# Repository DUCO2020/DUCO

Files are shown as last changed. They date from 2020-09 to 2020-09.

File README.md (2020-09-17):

DUCO

=======

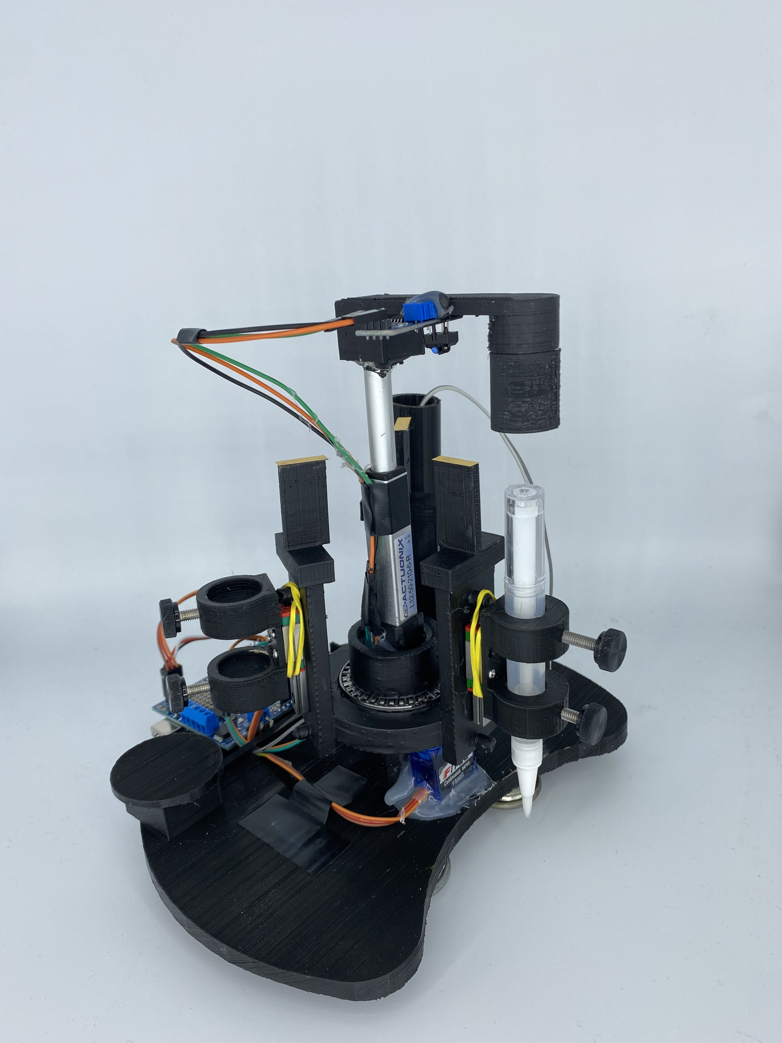
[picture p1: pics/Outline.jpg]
Art


DUCO is an open-source, tool switchable robotic system capable of drawing multi-layer circuits on versatile vertical surface. Assembling parts are highly accessible and low cost. It's inspired by Sandy Noble's work [*Polargraph*](https://github.com/euphy/polargraph)

DUCO is developed for large scale circuits fabrication, but maintaining considerable local precision and resolution. It has default optimal configuration for several drawing substrates - wall paper, glass, wood and etc, also supporting other substrate exploitation.

While linear actuator, laser cutter are well explored in this project, DUCO still have the extensible ability to welcomes all other tools like vinyl cutter and dispenser.

## High-level ability

* Two-stepper locomotion system with well set Cartesian-to-polar solution
* Meter size canvas
* Up to 3 tools mounting platform.
* Ink loaded pen based fabrication with good line quality
* Highly user extensible. User can explore any tools, inks and drawing substrates
* Autonomous robotic system with pen switch, pen pressure function enabled
* Enough spare GPIOs. User can develop new functions since only a few pins are occupied

## What we offer here

This resposity contains Graphical User Interface, Arduino operation firmware and all design files that our team used to test and explore this platform.

* **DucoFirmware** C code on [Arduino](https://www.arduino.cc/), currently supporting UNO to control all motion and actuation commands. 
* **DucoGUI** developed interface based on [Processing](https://processing.org/) framework, allowing user to interact with DUCO like selecting tools, uploading design files and start a drawing task.
* **DucoTest** contains all design files in SVG format that our team used.
* **DucoModels** gives access to all 3D model parts we used.
* **DUCO_BOM** inventory list.

## Put parts together

1. Before moving to run DUCO, you should first have all assembling parts ready. You can either use prototype files in Duco_models folder or design your own 3D model as long as you figure out the correct dimension for assembling.

2. After you get all these accessories printed, first thing you may want to do is assembling the centre platform, we have a figure that you can refer to when you do that.

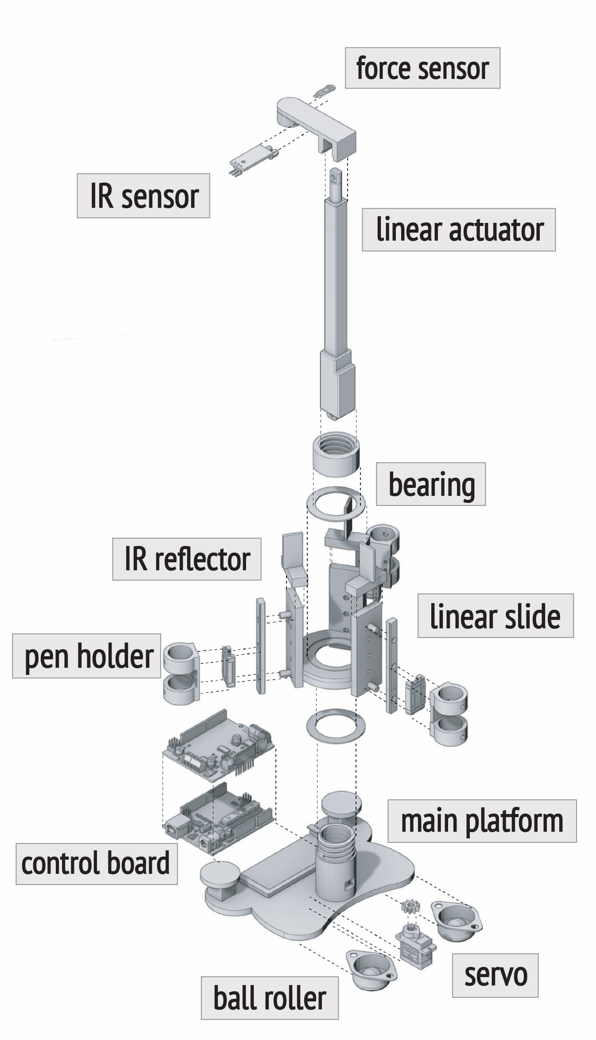
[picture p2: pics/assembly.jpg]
   

3. Subsequently, use hot glue to attach the printed anchor with your steppers( for our choice we use 4-wire [NEMA 17](https://www.banggood.com/3D-Printer-High-Torque-17-Stepper-Motor-300mN-1_5A-2-phase-4-wire-p-1064247.html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), it has a good rated current/ voltage about 5 volts which is suitable for a constant voltage driver.) Then you put a proper size of gear on the stepper driving axis for we need it to hang a belt.

## Hardware setup

1. The very first thing you need to do here is working out what size of your design is and choose a proper operiting area, after which you need to fix the two anchors on the top line. Remember to spare some space both horizontally and vertically, also collecting the dimensional data of your system

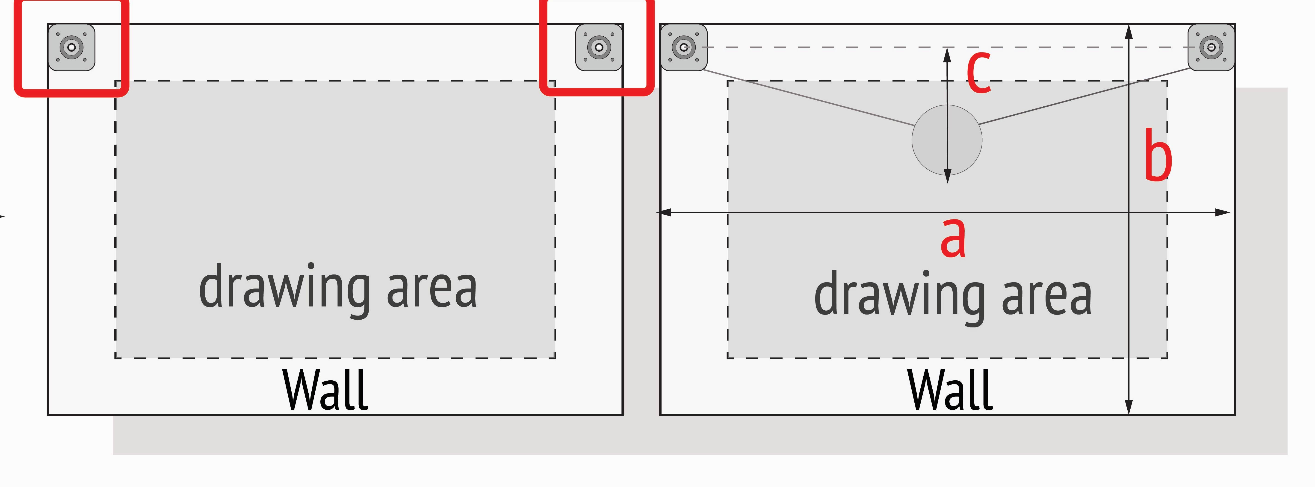
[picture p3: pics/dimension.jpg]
   

2. Moving forward, two [GT2 timing belts](https://www.amazon.com/Printing-Zeelo-Fiberglass-Rostock-Printers/dp/B0897CJKS1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) are involved. one end of each is both connected with center platform and the other one is tied to hold a weight. They are hanged on two anchors respectively. Note, choosing correct length is important, neither too short (not covering enough moving space) nor too long (causing loosen belts when the weight hits ground)

3. Now attach your Arduino Uno with motor shield. Our firmware is based on [Adafruit motor shield v2](https://learn.adafruit.com/adafruit-motor-shield-v2-for-arduino/overview), a typical constant voltage driver. If you want a more stable torque output, you may consider constant current driver AKA chopper driver. However using other shield requires you to modify the firmware configuration as well.

4. Uno and motor shield becomes control partner and you can stick them "in the brain" of our platform and also put metal stickers on the reflecters.

5. One last step you carrry out is to do wiring up

   - COMs on the shield: usually the stepper is together with 4-color wire, green/black is one couple, blue/red is another. each couple should be connected to one COM on the shield. One stepper is supposed to be connected to the same side's COMs, i.e. for one stepper COM1/2 are used, COM3/4 are responsible for another one.
   - Power port on the shield: + to 5V on DC, - to GND on DC
   - IR: Vcc to 5V on the shield, GND to GND on the shield, SIG to analog pin 1
   - Continuous servo:  to servo port 1 on the shield.
   - Linear actuator: to servo port 2 on the shield.
   - Arduino Uno: to your laptop with USB cable.

## Inventory 

We have an Excel table listing all materials that you may need.

## Q&A

1. Platform moving behavior is wrong.

   Probably something wrong with stepper wiring. Try to swap the connection that is under the same COM

2. When switching tool, the platform keeps rotating then stop and fails to locate a mounting slot.

   It's caused by unsuitable threshold set. Several reasons may result in this:

   - The metal sticker and the IR is not well aligned vertically
   - The metal sticker is not reflective enough
   -  Distance between IR and stickers is too far away.

   We recommend you to open an Arduino sketch and take a look at the IR feedback from analog pin 1. When sticker and IR are well aligned the value should be under 500, typically 200-350. If this is not your case, record your typical value and subtracted by 100-150. Then set this value to variables in Firmware: `thresholdxHigh`(x= 1,2,3) and try again.

   Note: three slots typical value should be almost the same (the program needs this assumption) and a good typical value is always much smaller than 1023. Adjust your `DEFAULT_UP_POSITION` in Firmware to achieve this.

3. Steppers are heating up.

   - The first thing you are looking into should be the supply voltage. Generally when it's higher than the rated voltage of your steppers, overheating takes place. Be sure to give correct voltage supply.
   - When the wires between two steppers and motor shield are not the same length. Wires are introducing extra resistance to your steppers, thus do your best to balance two wires' length(resistance)

4. Linear actuator shows no response or misbehaves.

   Basically caused by unstable connection between shield and linear actuator. Use some insulated tape to enhance the connection and make sure there's no other wires around that of linear actuator. Give it independent space since it's easy to be disturbed.

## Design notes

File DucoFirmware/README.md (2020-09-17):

# DUCOFirmware

This is the Arduino Uno folder that needed to be burnt in

## How to use it

- Download or clone this folder to your local. Make sure you get rid of the surfix "-master" generated by Github, since Arduino requires the folder name should match the main file name.
- connect your device to laptop, find the correct Serial Port on Arduino IDE "tools" sidebar. Then upload this Firmware into your device. At last make sure Arduino IDE is **NOT** occupying the Port after uploading, otherwise GUI Serial Port connection on Processing will fail.

## Functionality we provide

Refer to Section 5 of the paper

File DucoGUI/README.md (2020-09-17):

# DUCOGUI

This is the GUI folder for DUCO, it's based on Processing.

## How to use it

- Download or clone this folder to your local. Make sure you get rid of the surfix "-master" generated by Github, since Processing requires the folder name should match the main file name.
- If you have nothing to develop or tune, directly click on run. Then the interface will pop-up.

## Introduction to the Interface

- please refer to Section 6 of the paper

## Note

- photo paper/wood is a bit hard to fabricate circuits, so we enable Microstep. However, it's a super slow process without any speed control.
- Welcome page has a **Pen Position** menu. That part of functionality is not in use right now. It was aimed at making different mounting slots distinguishable by DUCO. However it requires different reflective stickers and responding different threshold set in Firmware. If you are interested in making it work, contact us!

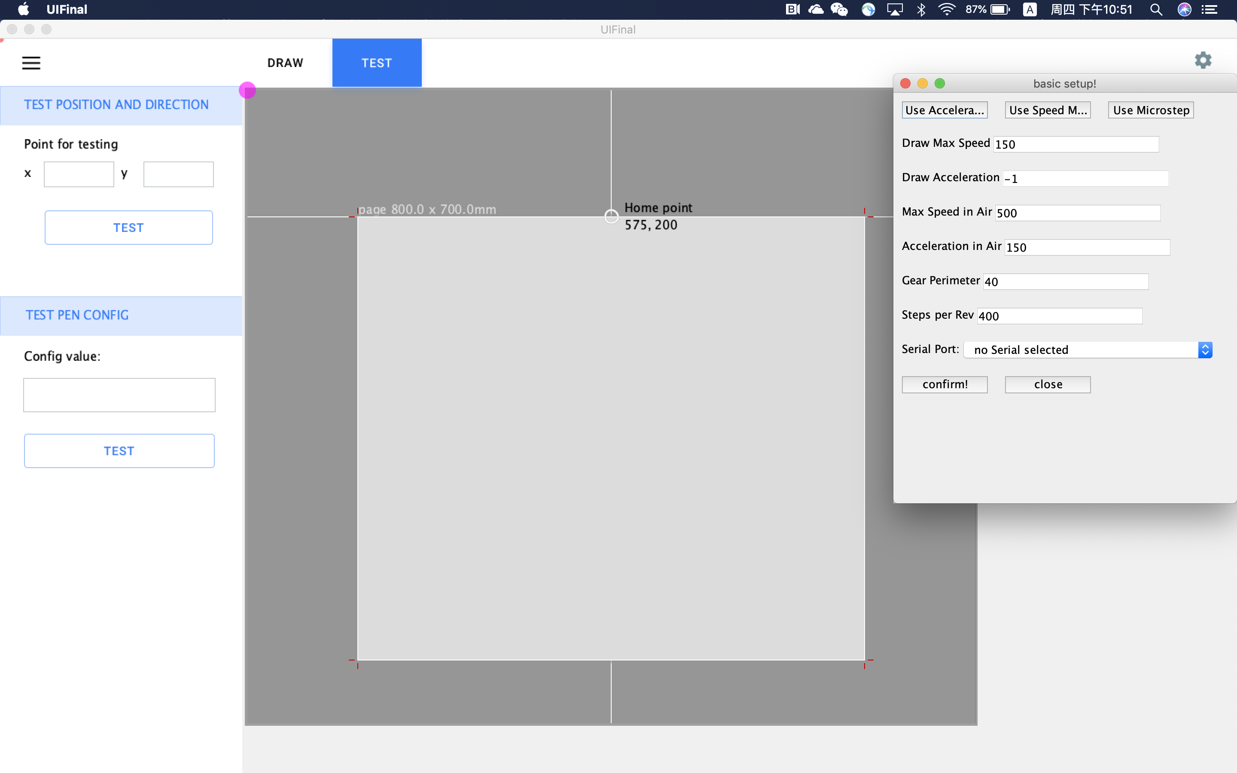
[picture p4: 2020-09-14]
DucoGUI/UI_Look/advancedSettings.png

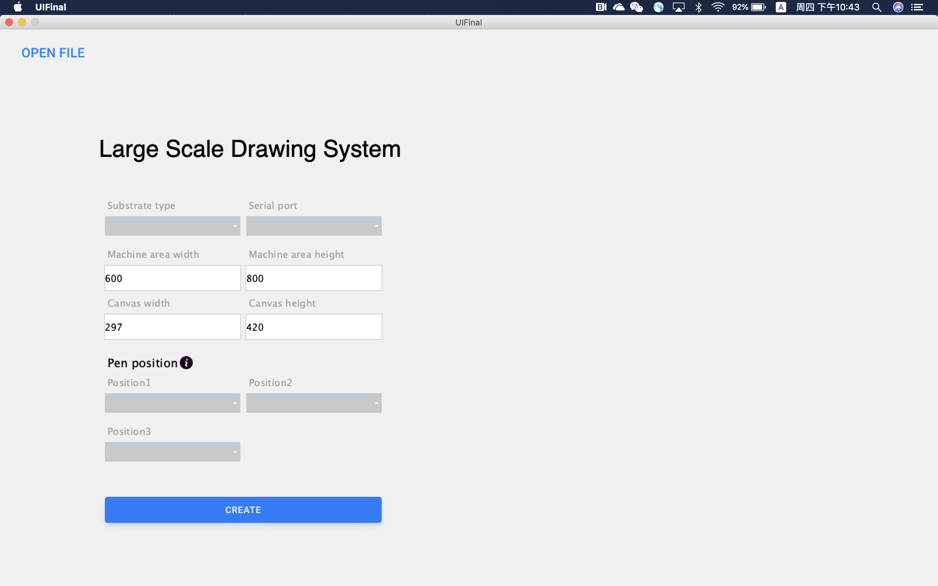
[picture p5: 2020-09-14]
DucoGUI/UI_Look/welcomePage.png

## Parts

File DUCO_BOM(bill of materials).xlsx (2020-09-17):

linear actuator | 1 | https://www.actuonix.com/L12-R-Linear-Servo-For-Radio-Control-p/l12-r.htm | 70 |  | L12 -R Micro Linear Servo - 50mm - 210:1 - 6 vdc
linear slide | 3 | https://www.amazon.com/gp/product/B07G3D6QHQ/ref=ppx_yo_dt_b_asin_title_o05_s00?ie=UTF8&psc=1 | 7.99 |  | LWL7B Miniature Linear Rail Guide 7mm Width Slide Block (40MM)
thumb nuts | 6 | https://www.mcmaster.com/catalog/126/3400 | 8.03/10 | 0.8each | Reinforced Plastic Knurled-Head Thumb Nuts 93886A230
thumb screw | 6 | https://www.mcmaster.com/catalog/126/3266 | 5.38/10 | 0.54 each | Metric Knurled Plastic-Head Thumb Screws 96016A559
continuous servo | 1 | https://www.amazon.com/gp/product/B079FRHBTR/ref=ppx_yo_dt_b_asin_title_o06_s00?ie=UTF8&psc=1 | 20.99/4 | 5.2 each | Geekstory Feetech FS90R 360 Degree Continuous Rotation Micro Servo Motor
rubber band | several | https://www.amazon.com/gp/product/B074B1KCXD/ref=ppx_yo_dt_b_asin_title_o01_s00?ie=UTF8&psc=1 | 5.49/bag |  | AmazonBasics 26543 Assorted Size and Color Rubber Bands
reflective paper | 1 | https://www.amazon.com/Silhouette-MEDIA-GLD-ADH-Printable-Gold-Foil/dp/B008RX1B28 | 9.64 |  | Silhouette Printable Gold Foil
jumper wire | several | https://www.amazon.com/gp/product/B07GD2BWPY/ref=ppx_yo_dt_b_asin_title_o02_s00?ie=UTF8&psc=1 | 5.79/120 |  | EDGELEC 120pcs Breadboard Jumper Wires 20cm
rotational bearing | 2 | https://www.mcmaster.com/catalog/126/1274 | 3.4 |  | Needle-Roller Thrust Bearings 5909K37
aruduino board (UNO) | 1 | https://www.amazon.com/Arduino-A000066-ARDUINO-UNO-R3/dp/B008GRTSV6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 | 22.79 |  | ARDUINO UNO R3
motor shield | 1 | https://www.amazon.com/gp/product/B00JI99DX4/ref=ppx_yo_dt_b_asin_title_o04_s01?ie=UTF8&psc=1 | 24.42 |  | Adafruit Motor/Stepper/Servo Shield for Arduino v2 Kit
force resistive sensor | 1 | https://www.tekscan.com/products-solutions/force-sensors/ess301 | 73.3/4 pieces | 18.325 | FlexiForce ESS301 Sensor
free weight | 2 | https://www.amazon.com/Ajax-Scientific-Economy-Hook-Weight/dp/B00EPQF4BK | 15.37 |  | Ajax Scientific ME180-0500 Economy Hook Weight, 500g
stepper motor | 2 | https://www.banggood.com/3D-Printer-High-Torque-17-Stepper-Motor-300mN-1_5A-2-phase-4-wire-p-1064247.html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 | 11.46 |  | High Torque 17 Stepper Motor 300mN 1.5A 2-phase 4-wire
IR sensor | 1 | https://www.amazon.com/gp/product/B07C69N65P/ref=ppx_yo_dt_b_asin_title_o00_s00?ie=UTF8&psc=1 | 12.99/10 piece | 1.3 each | OSOYOO 10PCS TCRT5000 Infrared Reflective IR Photoelectric Switch Barrier Line Track Sensor Module for Arduino Smart Car Robot with 5 8Pin Female to Female Jumper Wires
optional rollar | 2 | https://www.amazon.com/gp/product/B07ZHYFDW8/ref=ppx_yo_dt_b_asin_title_o03_s00?ie=UTF8&psc=1 | 10.99/8 | 1.37 each | MoKell 8pcs CY-15H 5/8-inch Bearing Steel Roller Ball
nano tape | 1 | https://www.amazon.com/gp/product/B07X32RKBN/ref=ppx_yo_dt_b_asin_title_o07_s00?ie=UTF8&psc=1 | 16 |  | GLUIT- Premium Nano Tape 17.5 lbs
belts | 1 | https://www.amazon.com/gp/product/B076LRL34G/ref=ppx_yo_dt_b_asin_title_o07_s00?ie=UTF8&psc=1 | 12.98 |  | SCStyle 10 Meters GT2 2mm Pitch 6mm Wide Timing Belt for 3D Printer CNC by SCStyle
silver nanoparticle ink | 1 | https://www.dycotecmaterials.com/product/dm-sij-3200/ | 428/100g |  | Dycotec DM-SIJ-3200 is a nanosilver ink-jet printable ink
dielectric ink | 1 | https://www.norlandprod.com/adhesives/NEA%20121.html | 47four onces |  | Norland Electronic Adhesive 121
pully | 1 | https://www.amazon.com/gp/product/B085QKS6X8/ref=ppx_yo_dt_b_asin_title_o03_s00?ie=UTF8&psc=1 | 12.99 |  | Befenybay 2Kit 2GT Synchronous Wheel Aluminum Timing Pulley with 2pcs Length 200mm Width 6mm Belt (20-48T-5B-6)
optional
laser cutter head 7W | 1 | https://www.amazon.com/gp/product/B088FJJ66M/ref=ppx_yo_dt_b_asin_title_o09_s00?ie=UTF8&psc=1 | 78 |  | NEJE 7W Engraving Module,2.5W Output Power,Suitable for NEJE Master 2 Engraving Machine,CNC Machine/Router/Arduino/3D Printer,etc.(2.5W Module)
laser cutting head 20W | 1 | https://www.amazon.com/gp/product/B088FGJBJ7/ref=ppx_yo_dt_b_asin_title_o09_s00?ie=UTF8&th=1 | 149 |  | NEJE 20W Engraving Module,5.5W Output Power,Suitable for NEJE Master 2 Engraving Machine,CNC Machine/Router/Arduino/3D Printer,etc.(5.5W Module)
pen | 1 | https://www.amazon.com/Montana-Cans-MXA324048-Acrylic-Marker/dp/B006ZM19IE | 4.25 |  | Montana Cans Montana Acrylic Empty, 2mm Paint Marker
brush | 1 | https://www.amazon.com/gp/product/B07W8T9CDQ/ref=ppx_yo_dt_b_asin_title_o00_s01?ie=UTF8&psc=1 | 9.98/12 | 0.83 | 12 Pack 3 ml Transparent Twist Pens
DV power supply | 1 | https://www.amazon.com/gp/product/B073TW8H2S/ref=ppx_yo_dt_b_asin_title_o05_s00?ie=UTF8&psc=1 | 69.99 |  | DC Power Supply Adjustable (0-30 V 0-10 A), Eventek KPS3010D Variable Switching Regulated Digital Power Supply
microscope | 1 | https://www.amazon.com/gp/product/B07PVMRZQH/ref=ppx_yo_dt_b_asin_title_o00_s00?ie=UTF8&psc=1 | 41.99 |  | Wireless Digital Microscope Handheld USB HD Inspection Camera
craft knife | 1 | https://www.dickblick.com/products/x-acto-1-knife/ | 4.16 |  | X-Acto #1 Knife
dispenser | 1
3D printed parts
main body_down | 1
mainbody_cap | 1
main body_up | 1
pen holder | 3
IR reflector | 3
linear actuator cap | 1
stepper holder

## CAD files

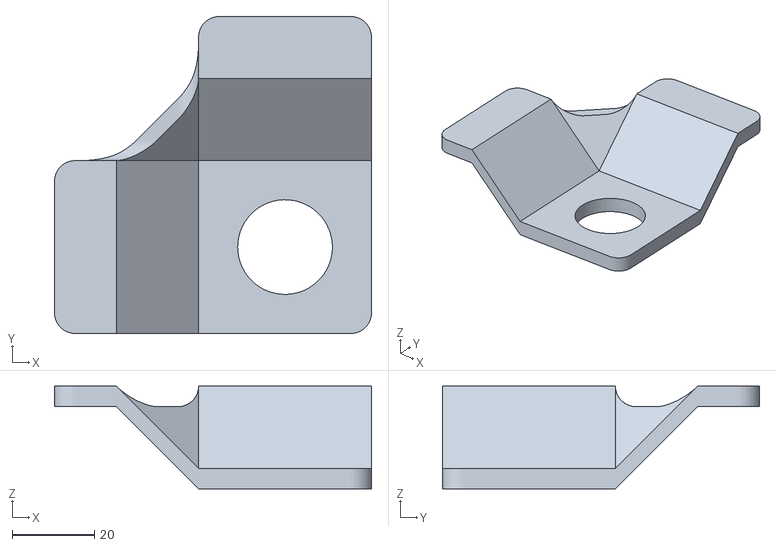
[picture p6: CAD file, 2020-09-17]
DucoModels/Steppermotor_holder.stl
77.0 x 77.0 x 25.0

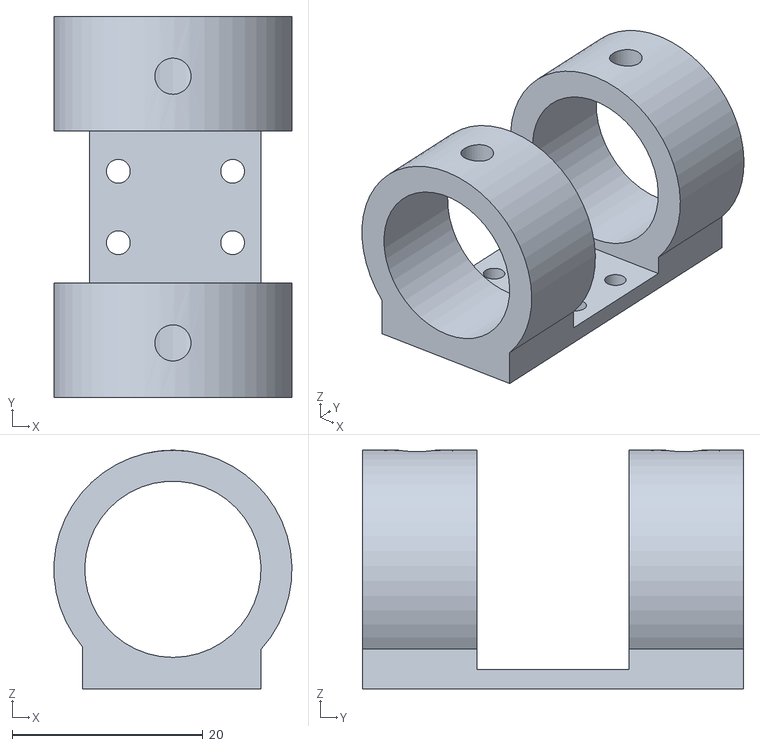
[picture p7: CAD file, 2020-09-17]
DucoModels/Pen_holder_big.STL
25.0 x 40.0 x 25.0

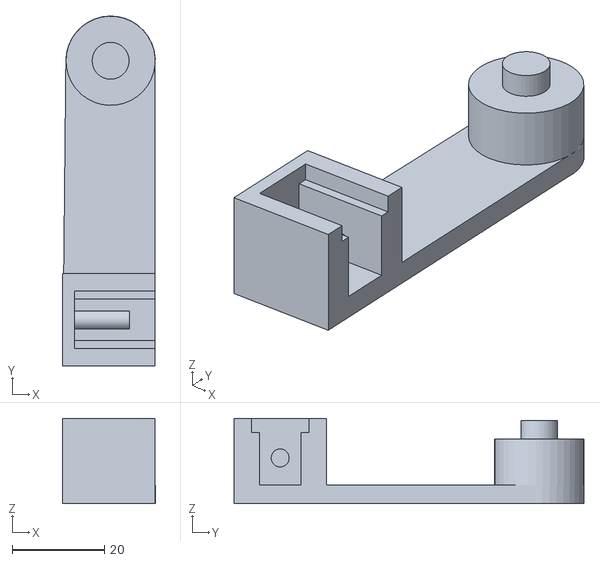
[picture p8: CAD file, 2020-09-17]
DucoModels/linearactuator_cap.STL
20.0 x 75.8 x 18.5

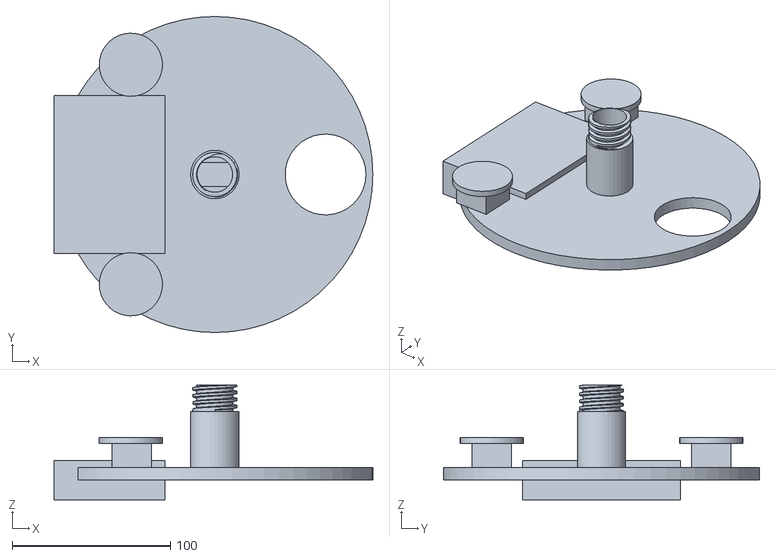
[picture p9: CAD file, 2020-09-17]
DucoModels/midplate_down_v2.STL
201.7 x 200.0 x 72.5

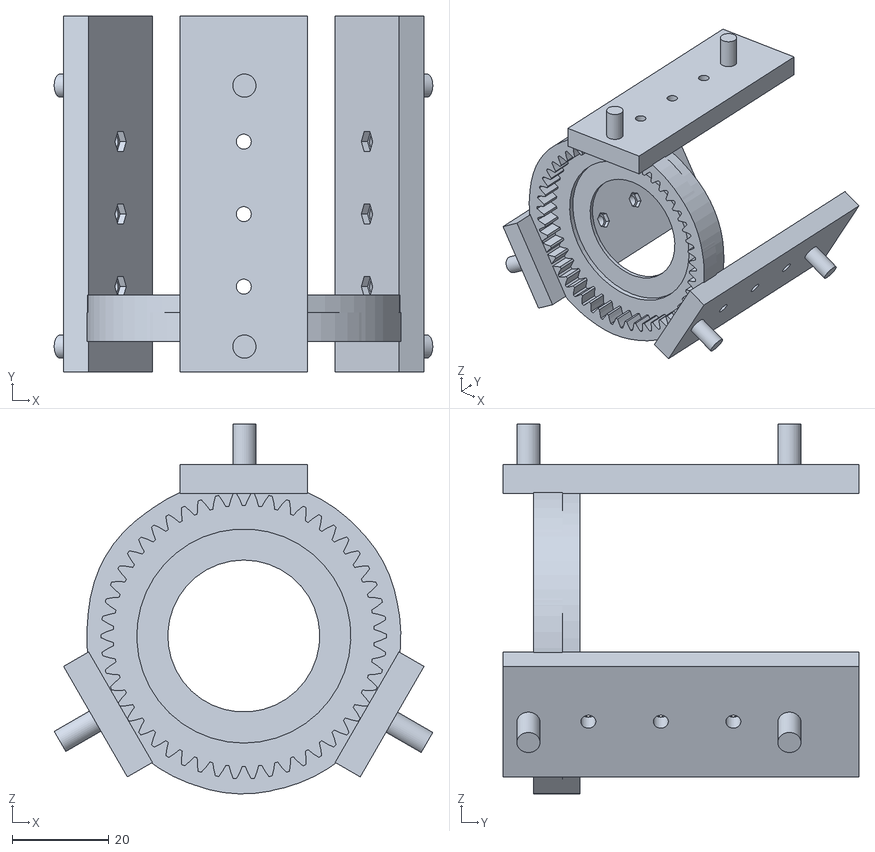
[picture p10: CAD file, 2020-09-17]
DucoModels/midplate_top.STL
78.3 x 73.7 x 76.5

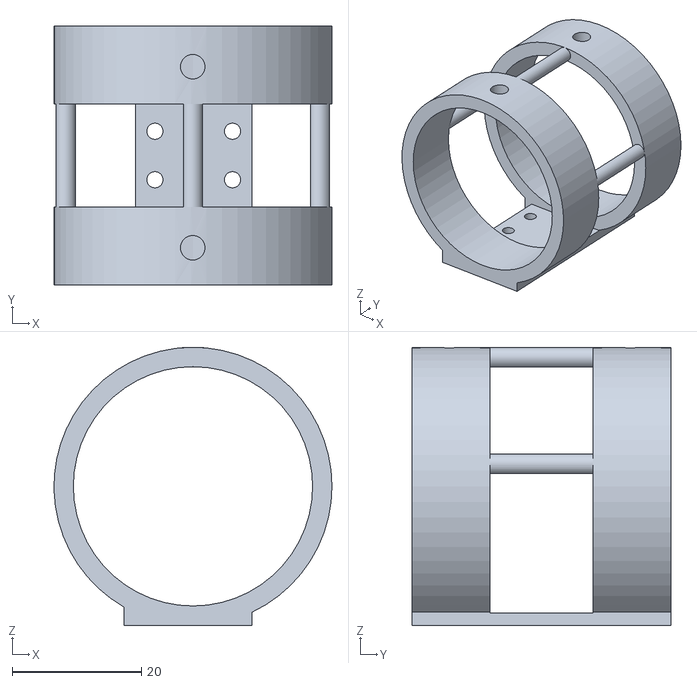
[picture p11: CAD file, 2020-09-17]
DucoModels/Microscope_holder.STL
43.0 x 40.0 x 43.0

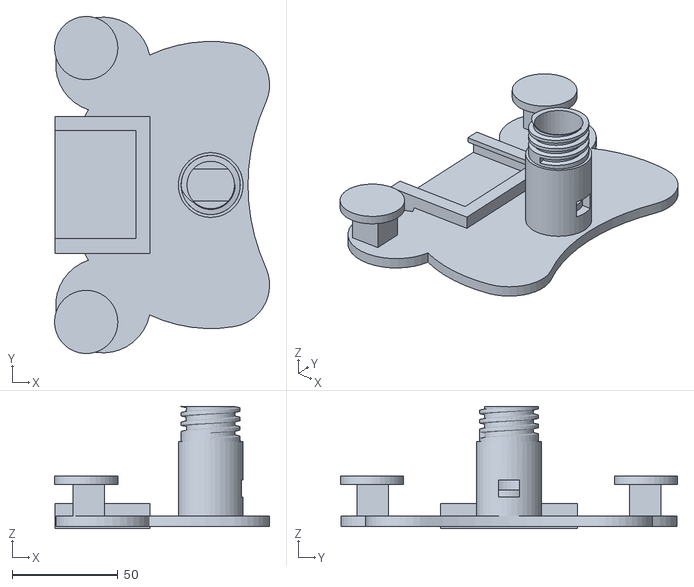
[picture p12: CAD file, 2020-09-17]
DucoModels/midplate_bottom_v1.STL
101.8 x 159.7 x 58.0

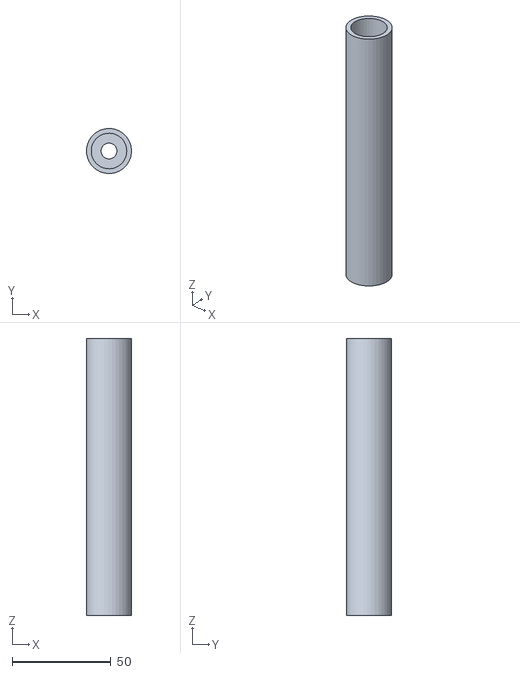
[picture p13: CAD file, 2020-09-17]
DucoModels/ultraviolet_holder.STL
22.8 x 22.8 x 140.0

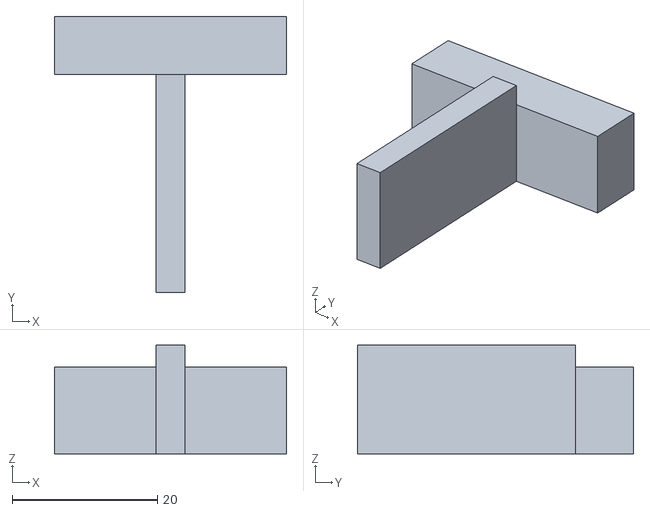
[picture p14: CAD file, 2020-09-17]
DucoModels/IRsensor_cap.STL
32.0 x 38.0 x 15.0

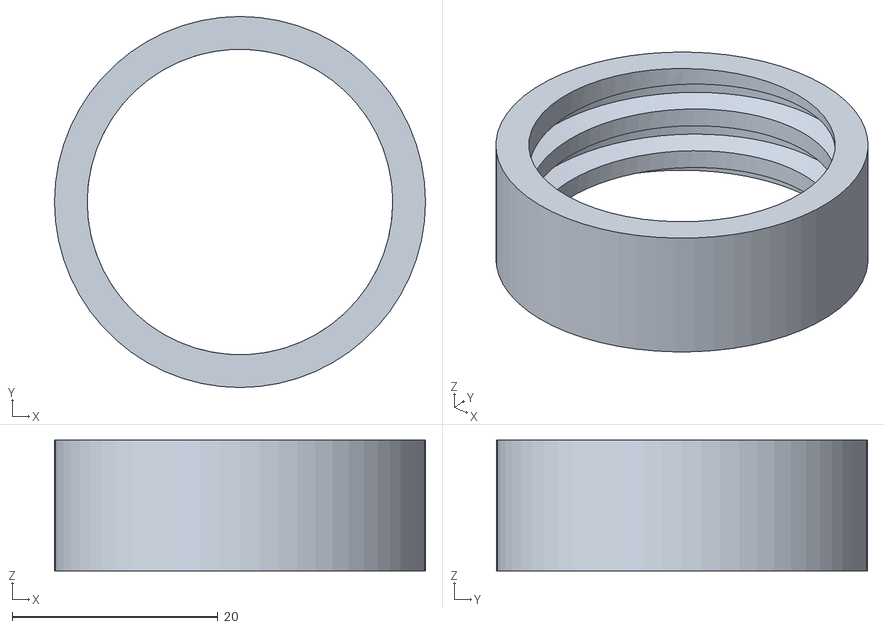
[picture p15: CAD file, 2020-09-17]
DucoModels/midplate_top_holder.STL
36.0 x 36.0 x 12.7

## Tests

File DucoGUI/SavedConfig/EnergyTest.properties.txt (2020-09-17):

#   ***  DUCO properties file   ***  
#Mon Sep 07 15:36:12 EDT 2020
DUCO.machine.width=1150
DUCO.homepoint.y=300
DUCO.page.width=800
DUCO.page.position.y=300
DUCO.motors.inAirMaxSpeed=500
DUCO.speedMode=1
DUCO.vector.position.y=280.75
DUCO.machine.height=1000
DUCO.motors.usingMicrostep=false
DUCO.vector.position.x=367.48
DUCO.motors.inAirAccel=150
DUCO.motors.maxSpeed=300
DUCO.motors.stepsPerRev=400.0
DUCO.motors.mmPerRev=40.0
DUCO.page.height=700
DUCO.motors.accel=100

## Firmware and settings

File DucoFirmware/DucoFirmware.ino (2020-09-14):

/**
*  DUCO - CORE
*  the main file to run this firmware
*  Make sure you have correct hardware setup and wiring
*  then this firmware works reliably
*/
#ifndef MICROCONTROLLER
#define MICROCONTROLLER MC_UNO
#endif
#define ADAFRUIT_MOTORSHIELD_V2
#include <Wire.h>
#include <Adafruit_MotorShield.h>
#define VECTOR_LINES
#define MC_UNO 1

#include <AccelStepper.h>
#include <Servo.h>
#include <EEPROM.h>
#include "EEPROMAnything.h"
const String FIRMWARE_VERSION_NO = "2";
//  EEPROM addresses
const byte EEPROM_MACHINE_WIDTH = 0;
const byte EEPROM_MACHINE_HEIGHT = 2;
const byte EEPROM_MACHINE_MM_PER_REV = 14; // 4 bytes (float)
const byte EEPROM_MACHINE_STEPS_PER_REV = 18;

const byte EEPROM_MACHINE_MOTOR_SPEED = 20; // 4 bytes float
const byte EEPROM_MACHINE_MOTOR_ACCEL = 24; // 4 bytes float

const byte EEPROM_MACHINE_HOME_A = 28; // 4 bytes
const byte EEPROM_MACHINE_HOME_B = 32; // 4 bytes

const byte EEPROM_PENLIFT_DOWN = 36; // 2 bytes
const byte EEPROM_PENLIFT_UP = 38; // 2 bytes

const byte EEPROM_PEN_MODE = 40; // 2 bytes int
const byte EEPROM_SPEED_MODE = 42; // 1 byte  only 2bits used
//const byte EEPROM_PLATFORM = 43;
/**
 *       SpeedMatch  Acceleration       utility
 * 00       false        false       microstepping
 * 01       false        true         Interleave
 * 10       true         false       under experiment
 * 11       true         true        under experiment
 */

int numberResend=0; // resend times counter
// motor setup
const int stepTypeM = MICROSTEP;  //resolution test
const int stepTypeI = INTERLEAVE;
int currentMotorMode = 0;

// Pen gesture control variables
Servo penHeight;
const int DEFAULT_PEN_MODE = 0;
const int DEFAULT_DOWN_POSITION = 1100; //pulse width in micro sec  
const int DEFAULT_UP_POSITION = 1750; // with new plugs
int upPosition = DEFAULT_UP_POSITION; // not used in PenMode 1
int downPosition = DEFAULT_DOWN_POSITION; // become percentage value in penMode 1
int penMode = DEFAULT_PEN_MODE; //0:linear actuator control; 1: laser cutter control; 2:pen force
static int penLiftSpeed = 110; // ms between steps of linear actuator
boolean isPenUp = true; // initial state should be up
byte const PEN_HEIGHT_SERVO_PIN = 10; //UNL2003 driver uses pin 9
byte const LASER_PIN = 3;

// pen force control
int safetyCheck = 1200;  // change along with different pen length/setup
int dynamicDownPos = DEFAULT_UP_POSITION; // used in penforce function
int ResHig = 1000; // high bound 150 Kohms with cheap FSR   600 with finer FSR
int ResLow = 100; // low bound 10 Kohms with cheap FSR   60 with finer FSR
const int power = 4;
const int FSR = 2;  // 0 is not reliable!!!!!

// platform rotate
Servo platRot;
boolean lastFound = false;
const int IR = 1;
byte const PLAT_ROTATE = 9;
const int Clockwise = 73;
const int stop = 90;
const int switchTimeout = 7000;
const int interval = 30;
const int weight = 0.3; // to guarantee fast response, not too large
int lastPer = 1000;
int threshold1High = 500; int threshold1Low = 0;  //tool1 with foil surface
int threshold2High = 500; int threshold2Low = 0;  //tool1 with foil surface
int threshold3High = 500; int threshold3Low = 0;  //tool1 with foil surface
//int threshold1High = 70; int threshold1Low = 0;  //tool1 with foil surface
//int threshold2High = 590; int threshold2Low = 560; //tool2 with white surface
//int threshold3High = 750; int threshold3Low = 720; //tool3 with black surface


// default values for wrong setup situation
static int defaultMachineWidth = 650;
static int defaultMachineHeight = 650;
static float defaultMmPerRev = 32;
static int defaultStepsPerRev = 200;
static int defaultSpeedMatch = false;
static int defaultusingAcceleration = true;
static float defaultMaxSpeed = 1000; // for Accel library one time setup
static float defaultMaxAcceleration = 800; // for Accel Library one time setup

// values used in RUNTIME
int machineWidth = defaultMachineWidth;
int machineHeight = defaultMachineHeight;
float mmPerRev = defaultMmPerRev; // 16*2=32 mm which is the default on Processing!
int motorStepsPerRev = defaultStepsPerRev; 
boolean speedMatch = defaultSpeedMatch;
boolean usingAcceleration = defaultusingAcceleration;
float currentMaxSpeed = defaultMaxSpeed;
float currentAcceleration = defaultMaxAcceleration;

int startLengthMM = 800;
float mmPerStep = mmPerRev / motorStepsPerRev; // perimeter divided by steps
float stepsPerMM = motorStepsPerRev / mmPerRev; // converter from mm to steps!!!!
long pageWidth = machineWidth * stepsPerMM;  //convert machine spec from mm to steps !!!
long pageHeight = machineHeight * stepsPerMM;
long maxLength = 0;
long StartPosA = 0;  // whenever run C09:SET HOME, HOME postion will be recorded here
long StartPosB = 0;

// command needed variable
const int INLENGTH = 50; // max length of a cmd
const char INTERMINATOR = 10; //cmd sequence inside terminator
const char SEMICOLON = ';';
static char inCmd[10]; // store cmd kind like "CXX" actually not used
static char inParam1[14]; // parse different parameters out of a string command
static char inParam2[14];
static char inParam3[14];
static char inParam4[14];
byte inNoOfParams; // number of parameters, at most 4
char lastCommand[INLENGTH+1]; // char[] storing cmd from Serial.read()
boolean commandConfirmed = false;

int rebroadcastReadyInterval = 5000;
long lastOperationTime = 0L;
long motorIdleTimeBeforePowerDown = 600000L;
boolean automaticPowerDown = false;  // no power down!!!
boolean powerIsOn = false;
boolean reportingPosition = true;
boolean currentlyRunning = true;
extern AccelStepper motorA; // refer to an extern variable defined in configuration
extern AccelStepper motorB;

long lastInteractionTime = 0L;
    

#define READY_STR "READY"
#define RESEND_STR "RESEND"
#define DRAWING_STR "DRAWING"
#define OUT_CMD_SYNC_STR "SYNC,"
char MSG_E_STR[] = "MSG,E,";
char MSG_I_STR[] = "MSG,I,";
char MSG_D_STR[] = "MSG,D,";

/*------- Processing communicates with arduino using these pre-set Commands --------*/
const static char COMMA[] = ",";
const static char CMD_END[] = ",END";
const static String CMD_CHANGELENGTH = "C01";
const static String CMD_CHANGESPEEDMODE = "C03"; // speed match or not use acceleration or not use Microstepping or not
const static String CMD_CHANGEMOTORMODE = "C04";
const static String CMD_SETPOSITION = "C09"; 

  /*--- Drawing task is mainly decomposed to C13/14/17 commands!! ----*/
  const static String CMD_PLAROTATE = "C11"; // platform rotate, fixing chosen pen at drawing slot
  const static String CMD_SWITCHPEN = "C12"; // switch to other pen control logic
  const static String CMD_PENDOWN = "C13";
  const static String CMD_PENUP = "C14";
  const static String CMD_SETPENLIFTRANGE = "C45"; // contains both Pen down&up position
  const static String CMD_CHANGELENGTHDIRECT = "C17";
  /*--- Drawing task is mainly decomposed to C13/14/17 commands!! ----*/

const static String CMD_SETMACHINESIZE = "C24"; 
const static String CMD_GETMACHINEDETAILS = "C26";
const static String CMD_RESETEEPROM = "C27";
const static String CMD_SETMACHINEMMPERREV = "C29";
const static String CMD_SETMACHINESTEPSPERREV = "C30";
const static String CMD_SETMOTORSPEED = "C31";
const static String CMD_SETMOTORACCEL = "C32";
/*------- Processing communicates with arduino using these pre-set Commands --------*/


void setup() 
{
  Serial.begin(57600);
  Serial.println("DUCO is ready");
  Serial.print("Hardware: ");
  Serial.println(MICROCONTROLLER);
  #if MICROCONTROLLER == MC_UNO
  Serial.println("MC_UNO");
  #else
  Serial.println("No MC");
  #endif
 
  eeprom_resetEeprom(); // reset EEPROM to be ready
  configuration_setup(); // default values setting not quite important
  // don't know why these settings are needed
  // but without them, stepper's speed is not controllable
  // i.e. setSpeed doesn't work
  motorA.setMaxSpeed(defaultMaxSpeed);
  motorB.setMaxSpeed(defaultMaxSpeed);
  motorA.setAcceleration(defaultMaxAcceleration);  
  motorB.setAcceleration(defaultMaxAcceleration);
  
  float startLength = ((float) startLengthMM / (float) mmPerRev) * (float) motorStepsPerRev; // mm to steps
  motorA.setCurrentPosition(startLength);
  motorB.setCurrentPosition(startLength);
  // INLENGTH max length of a command, set to null str
  for (int i = 0; i<INLENGTH; i++) {
    lastCommand[i] = 0;
  }

  comms_ready();

  
  // default pen up! && close laser cutter if used
  penlift_initial(1750); 
  penlift_laserCutterOff();
  delay(500);
}

void loop()
{
  if (comms_waitForNextCommand(lastCommand)) 
  {
    comms_parseAndExecuteCommand(lastCommand);
    // after this lastCommand has been reset
  }
}

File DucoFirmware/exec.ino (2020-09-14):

/**
*  DUCO - CORE
*  The main script to parse any incoming cmds
*/

boolean exec_executeBasicCommand(String &com)
{
  boolean executed = true;
  if (com.startsWith(CMD_CHANGELENGTH)) //C01 Move Pen To Point
    exec_changeLength();
#ifdef VECTOR_LINES
  else if (com.startsWith(CMD_CHANGELENGTHDIRECT)) // C17 draw a straight line
    exec_changeLengthDirect();
#endif
  else if (com.startsWith(CMD_SETMOTORSPEED))  //C31
    exec_setMotorSpeed();
  else if (com.startsWith(CMD_SETMOTORACCEL))  //C32
    exec_setMotorAcceleration();
  else if (com.startsWith(CMD_SETPOSITION))  //C09 SET HOME
    exec_setPosition();
  else if (com.startsWith(CMD_PENDOWN))  // C13 penDown
    penlift_penDraw();
  else if (com.startsWith(CMD_PENUP))  //  C14 penUp
    penlift_penRelease();
  else if (com.startsWith(CMD_SETPENLIFTRANGE))  // C45
    exec_setPenLiftRange();
  else if (com.startsWith(CMD_SETMACHINESIZE))  // C24
    exec_setMachineSizeFromCommand();
  else if (com.startsWith(CMD_SETMACHINEMMPERREV))
    exec_setMachineMmPerRevFromCommand();
  else if (com.startsWith(CMD_SETMACHINESTEPSPERREV))
    exec_setMachineStepsPerRevFromCommand();
  else if (com.startsWith(CMD_GETMACHINEDETAILS))
    exec_reportMachineSpec();
  else if (com.startsWith(CMD_RESETEEPROM))
    eeprom_resetEeprom();
  // new added function
  else if (com.startsWith(CMD_CHANGESPEEDMODE)) //C03
    exec_setSpeedMode(); 
  else if (com.startsWith(CMD_SWITCHPEN)) //C12
    exec_setPenMode();
  // new added function
  else if (com.startsWith(CMD_PLAROTATE))
    exec_platRotate();
  else if (com.startsWith(CMD_CHANGEMOTORMODE))
    exec_setMotorMode();
  else
    executed = false; // no basic command is executed

  return executed;
}

void exec_reportMachineSpec()
{
  eeprom_dumpEeprom();
  Serial.print(F("PGSIZE,")); // align with String.startsWith() in processing
  Serial.print(machineWidth);
  Serial.print(COMMA);
  Serial.print(machineHeight);
  Serial.println(CMD_END);

  Serial.print(F("PGMMPERREV,"));
  Serial.print(mmPerRev);
  Serial.println(CMD_END);

  Serial.print(F("PGSTEPSPERREV,"));
  Serial.print(motorStepsPerRev);
  Serial.println(CMD_END);

  Serial.print(F("PGLIFT,"));
  Serial.print(downPosition);
  Serial.print(COMMA);
  Serial.print(upPosition);
  Serial.println(CMD_END);

  Serial.print(F("PGSPEED,"));
  Serial.print(currentMaxSpeed);
  if(usingAcceleration){
    Serial.print(COMMA);
    Serial.print(currentAcceleration);
  }
  Serial.println(CMD_END);

  Serial.print(F("SPEEDMATCH:"));
  Serial.print(speedMatch? 1:0);
  Serial.print(COMMA);
  Serial.print(F("ACCEL:"));
  Serial.print(usingAcceleration? 1:0);
  Serial.println(CMD_END);

  Serial.print(F("PENMODE:"));
  Serial.print(penMode);
  Serial.println(CMD_END);
}



/*--- accept new values from inParams, store them into EEPROM and also reload to global variables---*/
// C04 interleave/microstepping change
void exec_setMotorMode(){
  byte motorMode = (byte) atoi(inParam1);
  // motor._speed/_maxSpeed/_accel/_position will all be set to zero
  if(motorMode != currentMotorMode){
    if(motorMode==0){
      motorA = AccelStepper(forwardaI, backwardaI);
      motorB = AccelStepper(forwardbI, backwardbI);
      Serial.println("Interleave choosen!");
    }
    if(motorMode==1){
      motorA = AccelStepper(forwardaM, backwardaM);
      motorB = AccelStepper(forwardbM, backwardbM);
      Serial.println("Microstepping choosen!");
    }
    currentMotorMode = motorMode;
    // don't know why these settings are needed
    // but without them, stepper's speed is not controllable
    // i.e. setSpeed doesn't work
    motorA.setMaxSpeed(defaultMaxSpeed);
    motorB.setMaxSpeed(defaultMaxSpeed);
    motorA.setAcceleration(defaultMaxAcceleration);  
    motorB.setAcceleration(defaultMaxAcceleration);
  }
}

// C03 speedmode change
void exec_setSpeedMode(){
  byte speedSelector = (byte) atoi(inParam1);
  EEPROM_writeAnything(EEPROM_SPEED_MODE,speedSelector);
  eeprom_loadSpeedMode(); // reload
  if(!usingAcceleration){
    EEPROM_writeAnything(EEPROM_MACHINE_MOTOR_ACCEL, -1); // not used
    eeprom_loadSpeed();  // reload speed and accel
  }
}

// C11 for platform rotate
void exec_platRotate(){
  int Selection = atoi(inParam1);
  if(Selection<=3 && Selection>=1){
    platformRotate(Selection);
  }
  else{
    Serial.println("Selection not valid!");
  }
}

// C12 pen switch
void exec_setPenMode(){
  int mode = atoi(inParam1);
  EEPROM_writeAnything(EEPROM_PEN_MODE,mode);
  eeprom_loadPenMode(); //reload
  switch(penMode){
    case 0:
      // reset to default
      EEPROM_writeAnything(EEPROM_PENLIFT_DOWN,DEFAULT_DOWN_POSITION);
      EEPROM_writeAnything(EEPROM_PENLIFT_UP,DEFAULT_UP_POSITION);
      eeprom_loadPenUpPosition(); // reload
      eeprom_loadPenDownPosition();//
      break;
    case 1:
      EEPROM_writeAnything(EEPROM_PENLIFT_UP,-1); //not used
      EEPROM_writeAnything(EEPROM_PENLIFT_DOWN,0); //set to lowest value
      eeprom_loadPenUpPosition(); // reload
      eeprom_loadPenDownPosition(); // reload
      break;
    case 2:
      // need change along with different pen length/setup
      EEPROM_writeAnything(EEPROM_PENLIFT_UP,1750);
      eeprom_loadPenUpPosition(); // reload
      dynamicDownPos = upPosition;
      break;
    default:
      break;
  }
}

// C24
void exec_setMachineSizeFromCommand()
{
  int width = atoi(inParam1); // machine width
  int height = atoi(inParam2); // machine height

  // load to get current settings
  int currentValue;
  EEPROM_readAnything(EEPROM_MACHINE_WIDTH, currentValue);
  if (currentValue != width)
    if (width > 10)
    {
      EEPROM_writeAnything(EEPROM_MACHINE_WIDTH, width);
    }
  
  EEPROM_readAnything(EEPROM_MACHINE_HEIGHT, currentValue);
  if (currentValue != height)
    if (height > 10)
    {
      EEPROM_writeAnything(EEPROM_MACHINE_HEIGHT, height);
    }

  // reload 
  eeprom_loadMachineSize(); // load from EEPROM to global variables - machineWidth & machineHeight
}
void exec_setMachineMmPerRevFromCommand()
{
  EEPROM_writeAnything(EEPROM_MACHINE_MM_PER_REV, (float)atof(inParam1));
  eeprom_loadMachineSpecFromEeprom();
}
void exec_setMachineStepsPerRevFromCommand()
{
  EEPROM_writeAnything(EEPROM_MACHINE_STEPS_PER_REV, atoi(inParam1));
  eeprom_loadMachineSpecFromEeprom();
}
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

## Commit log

2020-09-17 Adding pics and BOM
    [DUCO_BOM(bill of materials).xlsx]
2020-09-17 model folder created
    [IRsensor_cap.STL, Microscope_holder.STL, Pen_holder_big.STL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]
